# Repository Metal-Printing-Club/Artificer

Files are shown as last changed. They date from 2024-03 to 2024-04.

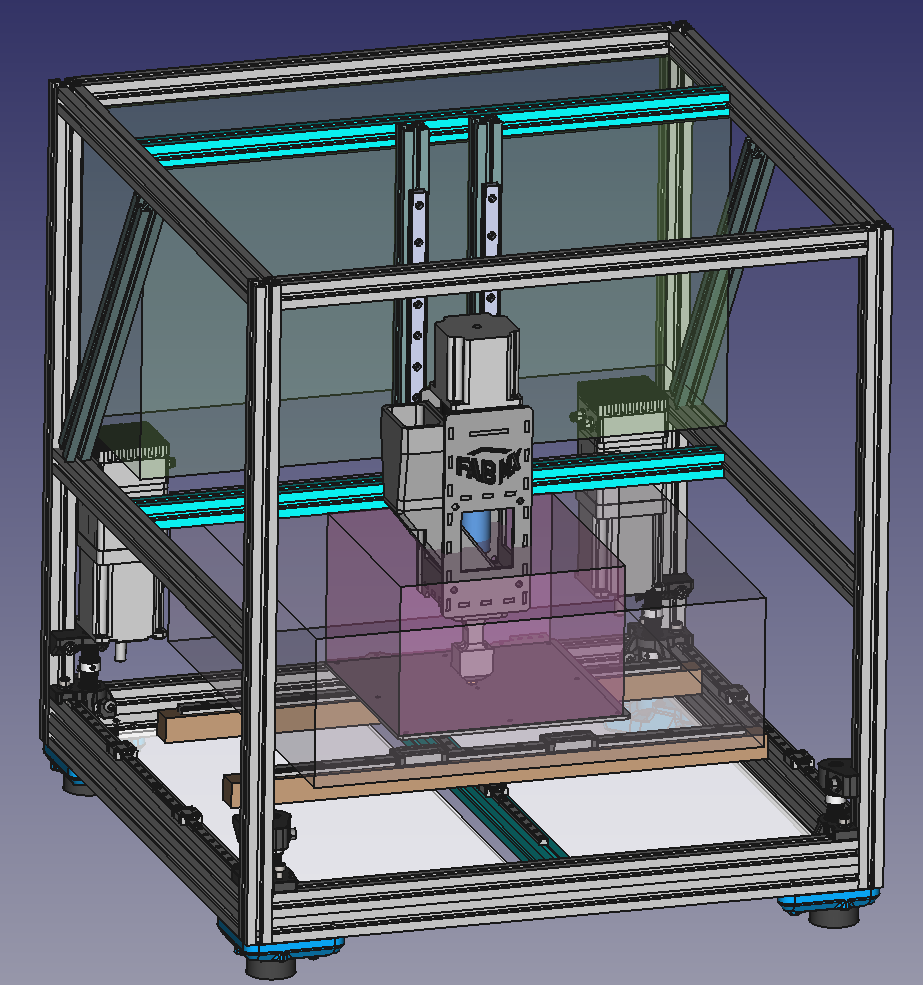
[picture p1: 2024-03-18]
printer-dev/Screenshot 2024-03-17 101501.png

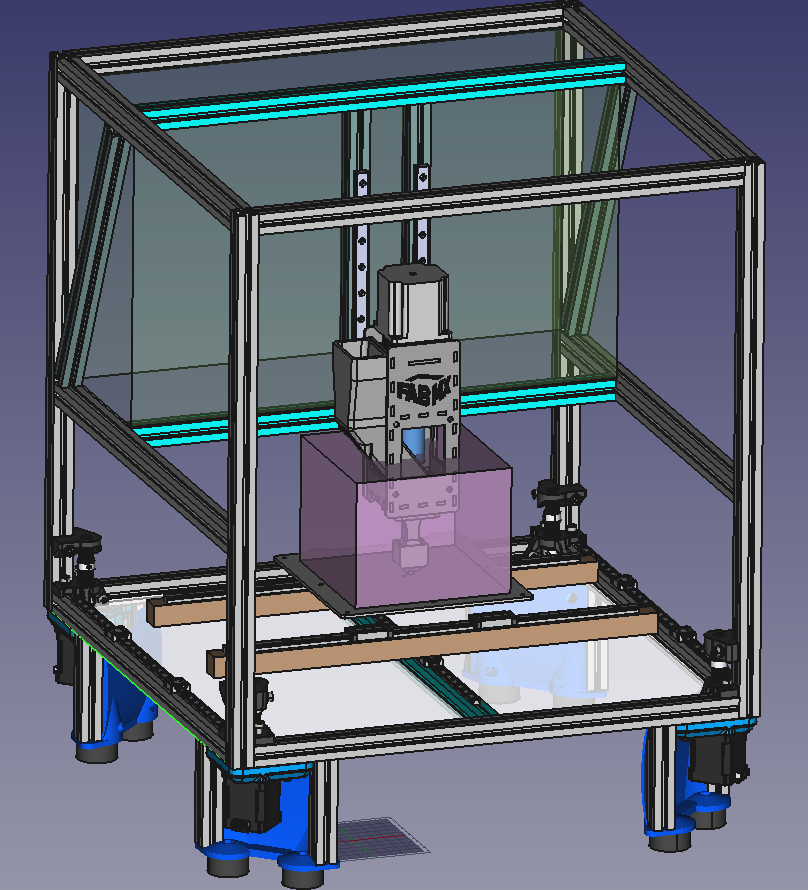
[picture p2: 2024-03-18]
printer-dev/Screenshot 2024-03-14 174216.png

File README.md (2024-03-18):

# Artificer

This is a 3D printer developed at Makespace in Cambridge.

It is primarily intended as a development platform for the FabMX extruder.

The goal is to deliver high precision motion when printing with a very heavy toolhead using affordable and readily-available parts.

We will steal as much as possible from other open hardware projects such as Voron.

The printer should have a build volume of at least 120mm cube. The printer must have a heated bed. Ideally, the printer should be enclosed. Water cooling of the extruder must be integrated. Print speed doesn't have to be world-beating but it would be nice if it was at least comparable to a modern, stock, "off the shelf" 3D printer such as a Voron 2.4.

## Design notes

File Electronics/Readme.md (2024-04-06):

The current electronics configuration for Artificer is as follows:

## Components

### Control
* Mainboard: [Duet 3 6HC v1.01](https://docs.duet3d.com/Duet3D_hardware/Duet_3_family/Duet_3_Mainboard_6HC_Hardware_Overview)
* Expansion: 2x [Duet 3 Motor23CL](https://docs.duet3d.com/en/Duet3D_hardware/Duet_3_family/Duet_3_Motor_23CL)
* Display : [Paneldue 5i](https://docs.duet3d.com/Duet3D_hardware/Accessories/PanelDue)

### Motion

* Extruder Motor: 23HS22-2804S-PG15
* Z motor: 23HE22-2804S
* A/B Motors: Duet 3 Motor 23CL
* XY endstop: Voron Microswitch XY Endstop PCB
* Z endstop: Zmax limit swithc model TBC
* Nozzle touch off switch: Voron Sexbolt
* Z probe: _details TBC_

### Heating

* Extruder Heaters: 2x Generic 6x30-24V 40W, controled as 1x 80W heater
* Extruder thermistor: MF52B 100K B3590

### Cooling
* Extruder Coldside cooling: 12V water pump _details TBC_
* Part cooling blower : _details TBC_
* Electornics bay cooling: _details TBC_
* Other cooling: _details TBC_

##Wiring

The Duet 3 6HC wiring diagram is available on Duet 3D's documentation site, use the v1.01 version:
https://docs.duet3d.com/Duet3D_hardware/Duet_3_family/Duet_3_Mainboard_6HC_Hardware_Overview#wiring-diagram

reproduced below


Annotated image to follow, for now connect as follows:
### Power
* VIN 24V
* Jumper 24V to heated ben (OUT0) input

### Stepper Drivers
* Z Motor on Driver 0
* E motor on Driver 1
* A/B motos on CAN -Fd bus

### Heaters
* Heated bed OUT0
* Both extruder heater cartidges: OUT1
* heated bed thermistor: temp0
* extruder thermistor: temp1

### Endstops
* X : io2.in and GND
* Y : io3.in and GND
* Z : io4.in and GND

### PanelDue
* IO0 header (UART)

### Fans
TBC
Both banks of fan outouts can be set to 12V however NB 800mA max current draw

### Pump
Always on for now

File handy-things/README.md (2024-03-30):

# Handy things

Source and credits:

PanelDue 5" with PCB version 2 by Morten Nielsen found on https://grabcad.com/library/paneldue-5-with-pcb-version-2-1

Duet3D Nema23 closed loop stepper motor without brake 23CL_v1.0_M23-76-2804 by Tony Lock found at https://github.com/Duet3D/Duet3-M23CL/blob/master/v1.0/23CL_v1.0_M23-76-2804.step

FabMX Extuder v3.1 by FabMX found at https://wikifactory.com/+fabmxteam/fabmx/file/PelletExtruder/Version3.1/PelletExtruderv3.1.step

Voron Trident 350 by Voron Design et al. found at https://github.com/VoronDesign/Voron-Trident

Annex Engineering Gasherbrum k3 by Annex Engineering et al. found at https://github.com/Annex-Engineering/Gasherbrum-K3

Prusa Mini by Prusa3d found at https://github.com/prusa3d/Original-Prusa-MINI

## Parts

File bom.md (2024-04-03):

# Bill Of Materials (WIP!)

## Extruder

FabMX kit plus printed parts plus...
2x30mm 24V heater
Thermistor
V6 nozzle hardened steel

## Frame

Voron 2.4 350mm frame kit LDO

Allows us to use the full electronics bay, skirts, feet, etc from Voron Trident 350, so BOM for that (e.g. DIN rails etc) as stock.

Additional extrusions:
4x2040 470mm tapped
4x2020 310mm

Lots of plastic

## Electronics

Meanwell LRS-350-24
Meanwell LRS-200-24
Meanwell LRS-50-12
(Meanwell LRS-50-5? Only needed if we add a Pi)

DC-DC SSR (The second 24V PSU is for a heated bed, so that will be controlled with this)

Filtered fused IEC13 mains inlet
240V rocket switch

Duet3D 6HC controller board
(Duet3D toolhead board?)
Duet3D Paneldue 5i

Optional Raspberry Pi and/or controller board from other kits for Klipper experiments (or just to manage the water cooling? Or can we handle that from the Duet board?)

## Water cooling

Chinese water cooling kit, 240x120 radiator, integrated pump/tank, 12V PSU, 2x120mm 12V fan

Pump and tank:

https://www.aliexpress.com/item/1005004210851438.html?spm=a2g0o.order_list.order_list_main.95.61b31802qJqItj

This has a molex connector, like for a PC.

Specification:

Interface: 8mm/0.31" (used for internal diameter: 5.5-6.5mm/0.21-0.25" hose)
Threaded threads: G1/4
Model: water pump
Voltage: 12V
Power power: 19W
Water flow: 800L/h
Lift: 5m/16.4ft
Size:
Water tank +160MM: approx. 83mm+160mm/3.26+6.29"; Whole length: 264mm/10.39"
Outer diameter: 50mm/1.96"
Internal diameter: 40mm/1.57"

240mm radiator:

https://www.aliexpress.com/item/1005003018063623.html?spm=a2g0o.order_list.order_list_main.101.61b31802qJqItj

This has mounting points for fans and a couple of 1/4 inch threaded hose connectors.

2 x GDSTIME 12v 120mm fan

4 x screw to mount radiator to frame.  6-32 imperial thread.  20mm?

8 x screw to mount fans to radiator.  6-32 imperial thread.  30mm?

Tubing, jubilee clips, 1/4mm adapters, 8mm adapters, etc...

## Motors

XY Motors:
Nema23 - using Duet3D "Duet 3 Motor23 CL" (without brake)

Z motor:
Generic Nema 23

Extruder motor:

Like this from StepperOnline:

    Manufacturer Part Number: 23HS22-2804S-PG47
    Motor Type: Bipolar Stepper
    Step Angle: 0.039deg
    Holding Torque without Gearbox: 1.25Nm(177.01oz.in)
    Rated Current/phase: 2.8A
    Phase Resistance: 0.9ohms
    Inductance: 2.5mH ± 20%(1KHz)

Gear box between this (1:47) or as low as 1:10.

Can probably use a gear ratio as low as 1:2 safely with PolyMIM but we overspec this to experiment with other materials confidently.

## Bed

Prusa Mini 24v heated bed (magnetic, with integrated PCB heater and flat surface)
Prusa mini removeable PEI coated flexible steel sheet

## Motion

X:

Voron 430mm carbon fiber gantry tube x 2
Fysetc hollow rail MGN9 400mm x 2 + MGN9H carriage x 3

y:

400mm MGN7 x 3 + MGN7C carriage x 6

Need to design a special mounting part to attach these rails to the 2020 extrusions.

9mm belts in "Voron belt path" but with strange tensioning and motor mounts and very strange carriage.

z:

250mm MGN12H x 2
250mm lead screw et al.

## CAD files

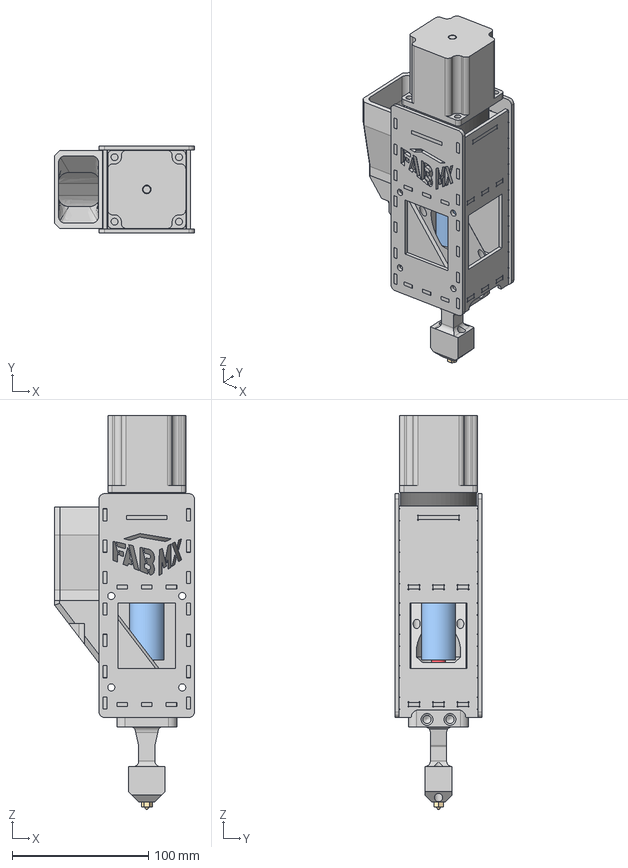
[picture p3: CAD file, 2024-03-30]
handy-things/PelletExtruderv3.1.step
102.7 x 64.0 x 288.8 mm
1fe10484-9e8a-11ee-95c5-028037ec0200_part
1fe12b84-9e8a-11ee-9896-028037ec0200_part
1fe12b85-9e8a-11ee-919e-028037ec0200_part
1fe12b86-9e8a-11ee-9747-028037ec0200_part
1fe12b87-9e8a-11ee-9325-028037ec0200_part
1fe12b88-9e8a-11ee-9519-028037ec0200_part
1fe12b89-9e8a-11ee-aabd-028037ec0200_part
1fe12b8a-9e8a-11ee-bf9c-028037ec0200_part
1fe12b8b-9e8a-11ee-9e8c-028037ec0200_part
PelletInlet_Funnel
E3D V6 Nozzle (0.4mm)
NEMA23 Motor
Getriebe
ShaftCoupler
10mm Extruder Screw (nicht exakt)

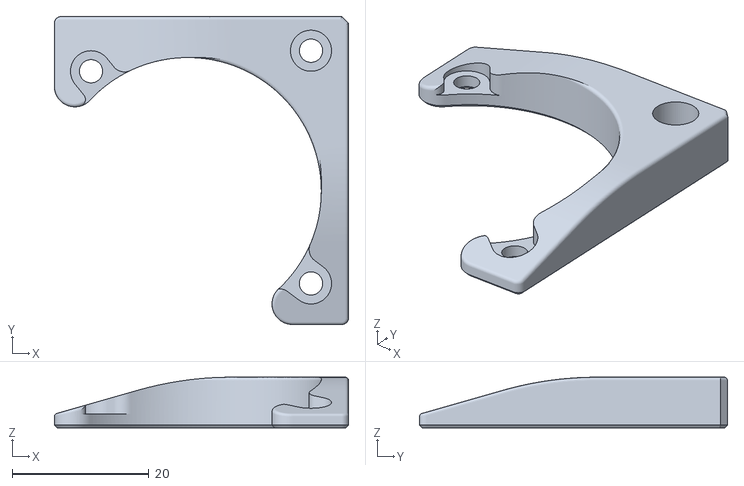
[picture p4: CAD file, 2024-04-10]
printer-dev/subassemblies/feet/[a]_corner_baseplate_a_x2.stl
43.0 x 45.0 x 7.40

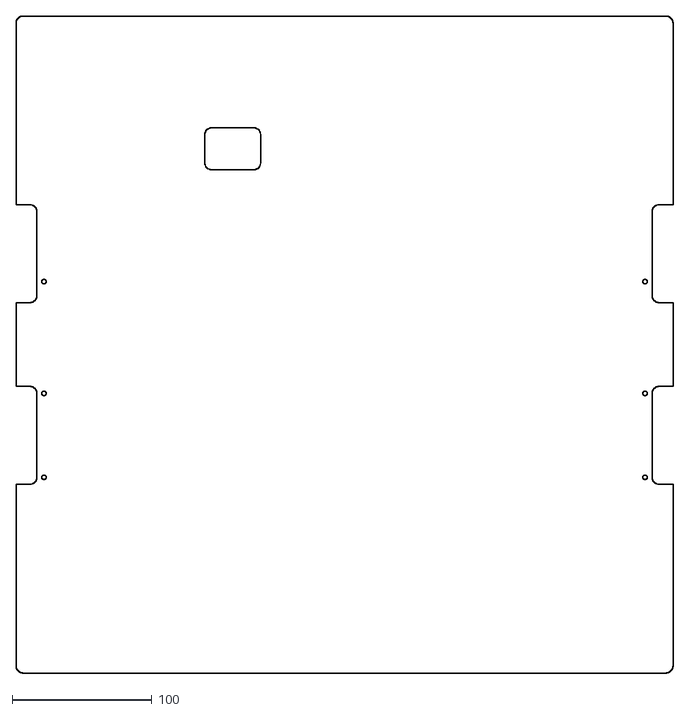
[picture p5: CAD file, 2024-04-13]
printer-dev/subassemblies/panels/deck.dxf
470.0 x 470.0

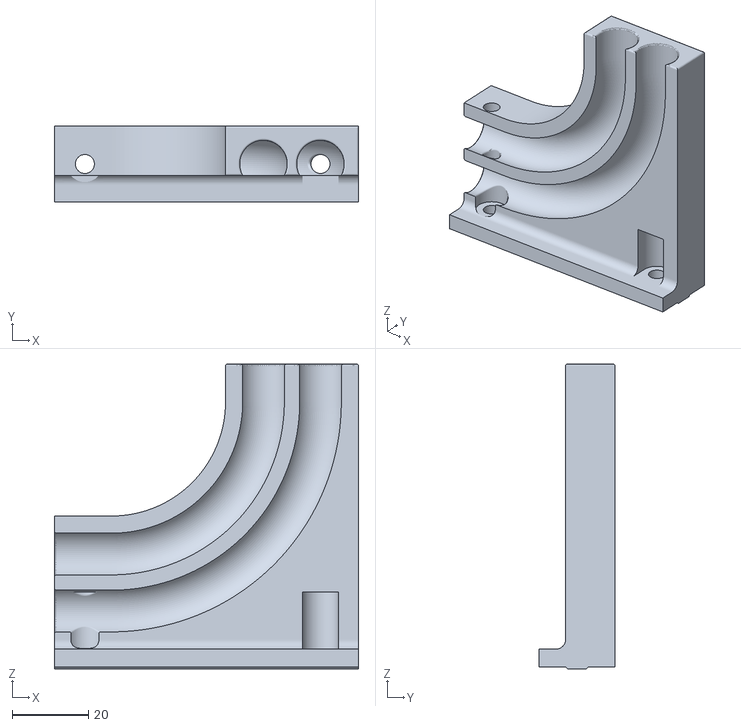
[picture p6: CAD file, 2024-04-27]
printer-dev/subassemblies/watercooling/PipeMountAndBend.stl
80.0 x 20.0 x 80.2

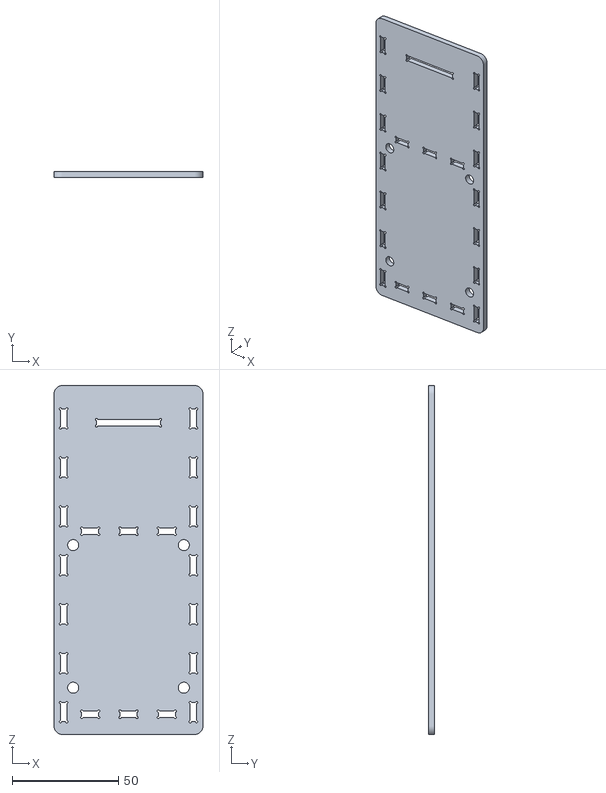
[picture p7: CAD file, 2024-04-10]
printer-dev/subassemblies/z/cad/mock_extruder-back.stl
70.0 x 3.00 x 164.0

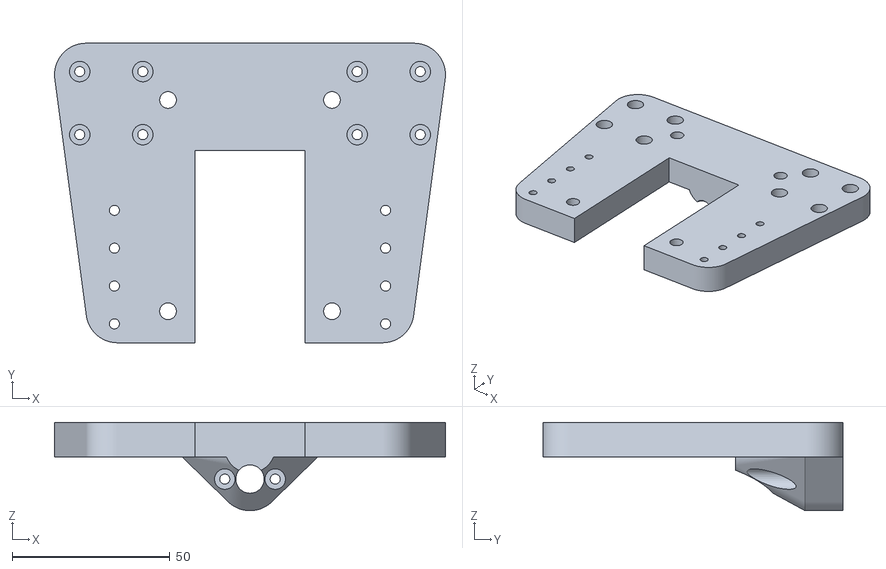
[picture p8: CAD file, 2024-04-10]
printer-dev/subassemblies/z/z-carriage-v2.stl
124.0 x 95.0 x 28.0

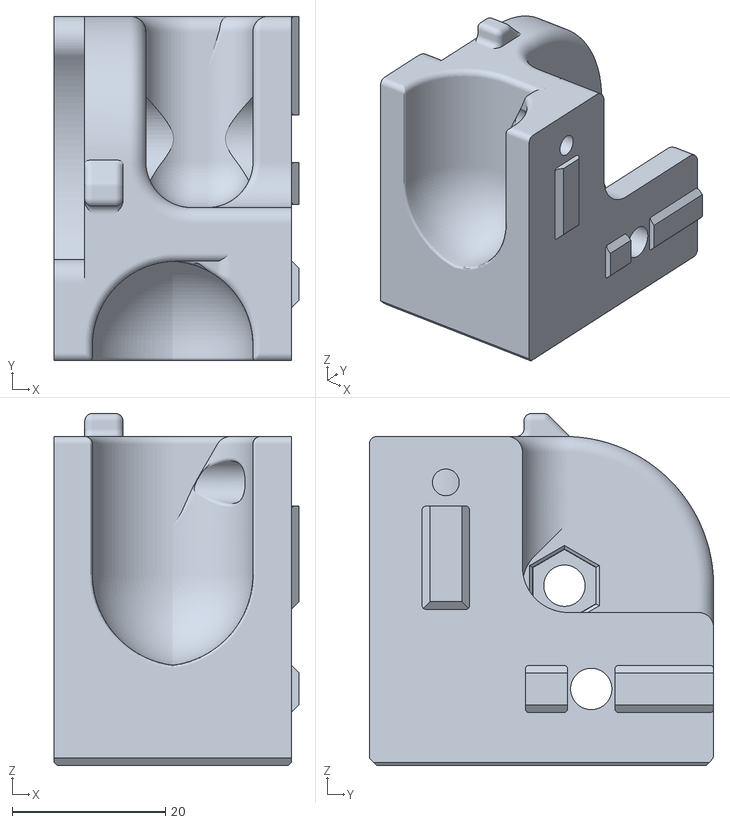
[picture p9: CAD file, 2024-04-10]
printer-dev/subassemblies/feet/corner_a_mod.stl
32.0 x 45.0 x 46.0

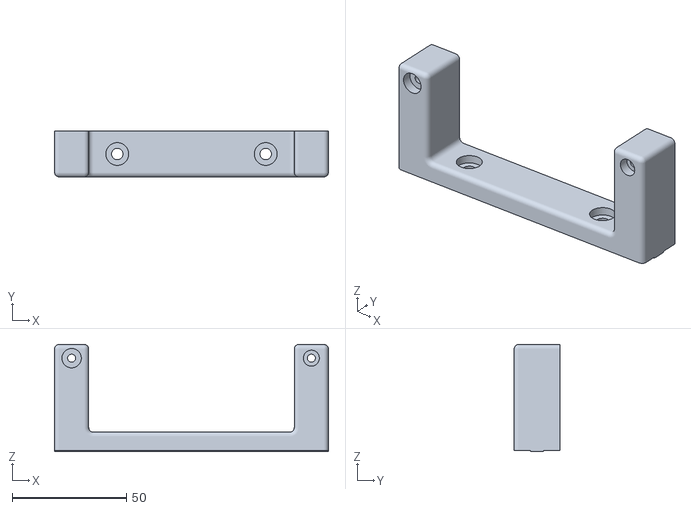
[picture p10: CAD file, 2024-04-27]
printer-dev/subassemblies/watercooling/RadiatorBottom.stl
120.0 x 20.0 x 46.9

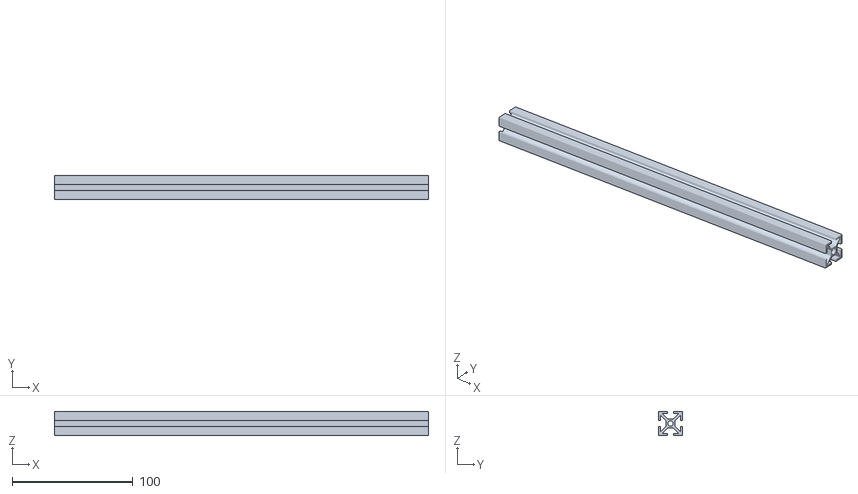
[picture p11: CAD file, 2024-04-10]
printer-dev/subassemblies/z/cad/mock_310-vert.stl
310.0 x 20.0 x 20.0

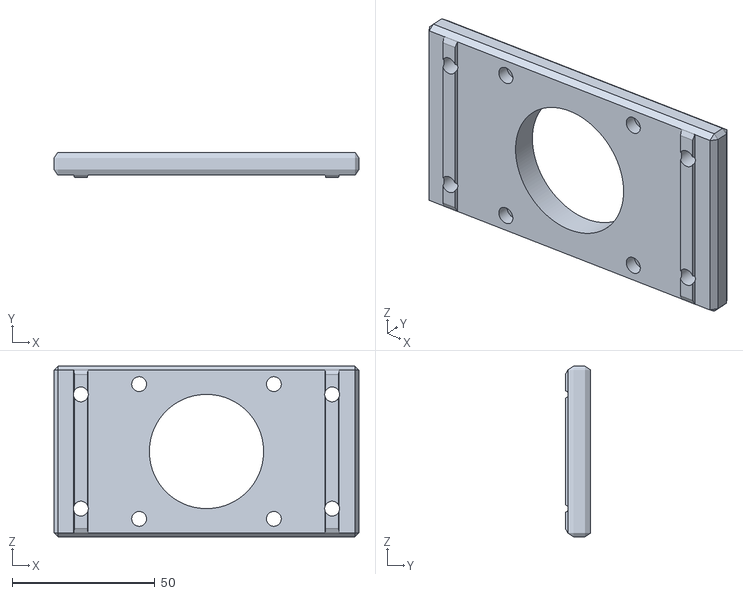
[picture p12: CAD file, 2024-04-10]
printer-dev/subassemblies/z/z-motormount-v2.stl
106.8 x 8.85 x 59.8

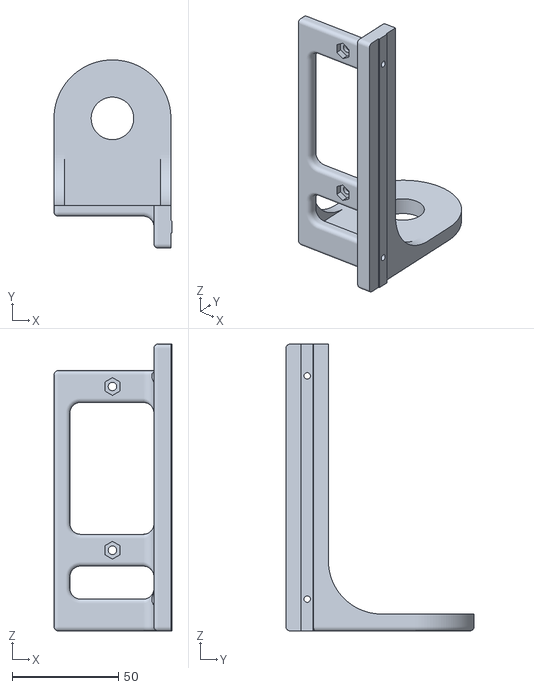
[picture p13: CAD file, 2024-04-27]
printer-dev/subassemblies/watercooling/WaterPumpMount.stl
55.5 x 88.5 x 135.0

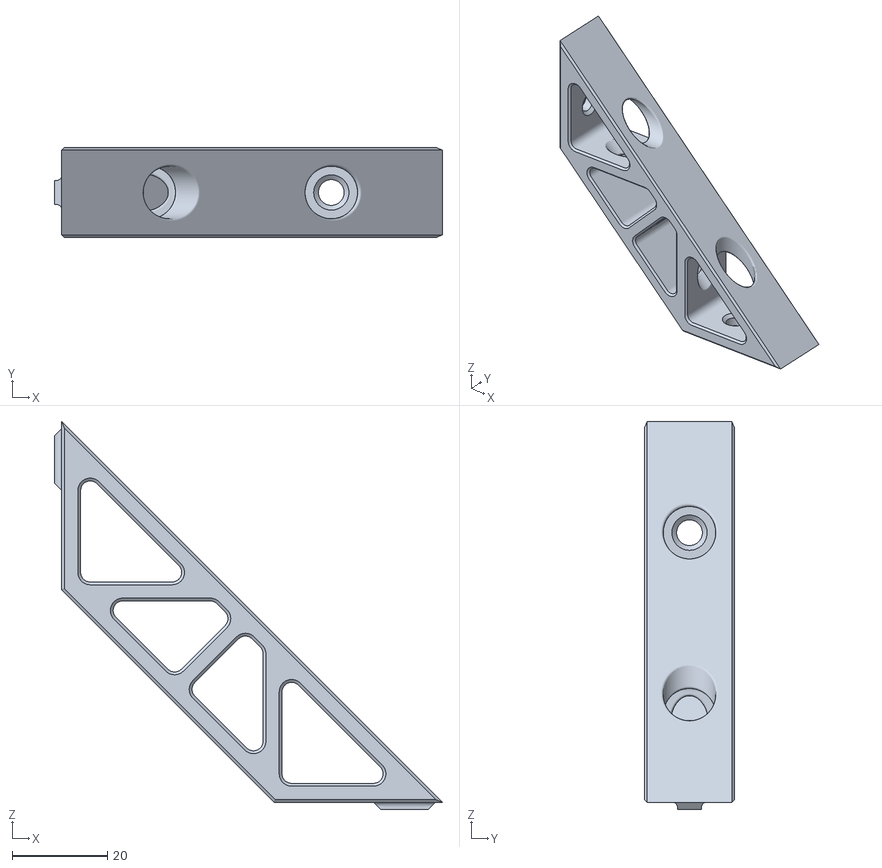
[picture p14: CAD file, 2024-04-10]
printer-dev/subassemblies/z/2020 Bracket.stl
81.5 x 19.0 x 81.5

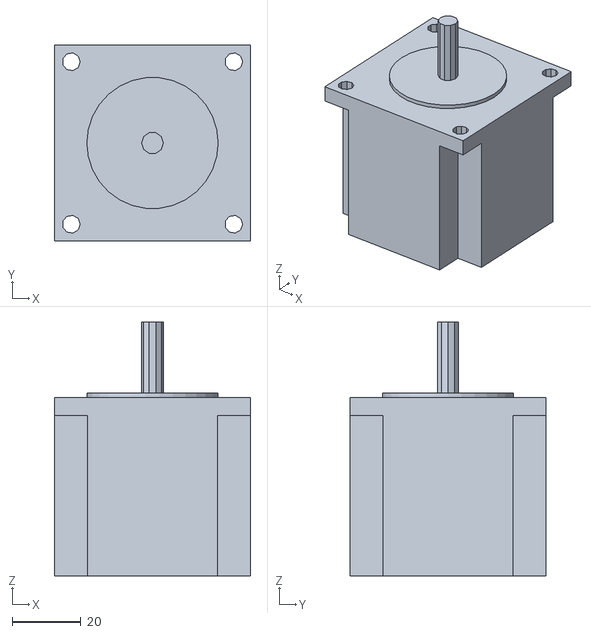
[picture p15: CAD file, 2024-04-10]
printer-dev/subassemblies/z/cad/mock_NEMA23.stl
56.9 x 56.9 x 73.7

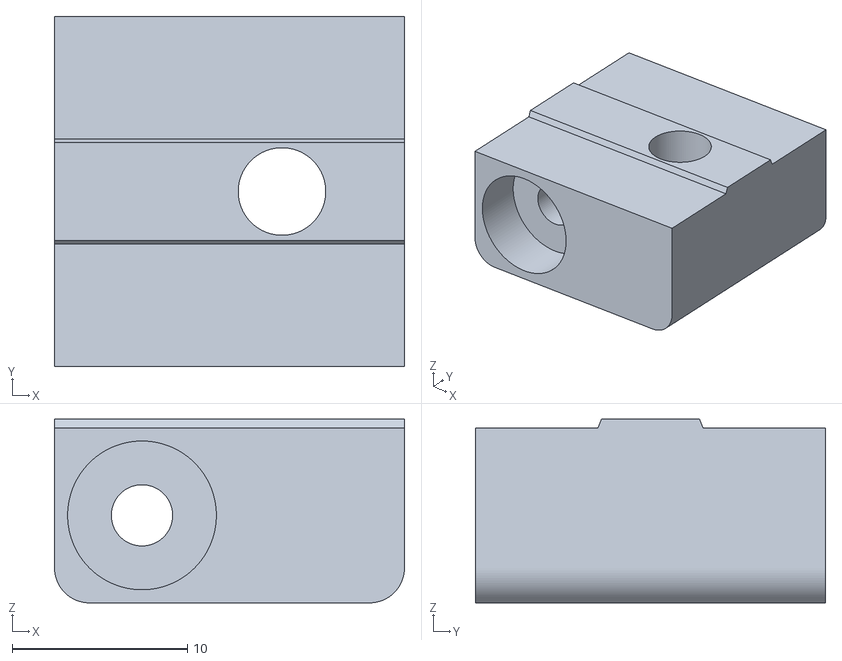
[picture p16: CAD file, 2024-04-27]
printer-dev/subassemblies/watercooling/RadiatorTop.stl
20.0 x 20.0 x 10.5

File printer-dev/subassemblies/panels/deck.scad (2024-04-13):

projection(cut = false) {

//translate([-20,-152.5,185])
//rotate([0,90,0])
//import("corner_a_x2.stl");
difference() {
hull() {
translate([-230,-230,0])
color("pink")
cylinder(d=10,h=2,$fn=64,center=true);

translate([230,230,0])
color("pink")
cylinder(d=10,h=2,$fn=64,center=true);

translate([-230,230,0])
color("pink")
cylinder(d=10,h=2,$fn=64,center=true);

translate([230,-230,0])
color("pink")
cylinder(d=10,h=2,$fn=64,center=true);
}

translate([-215,-35 - 60,0])

cylinder(d=3.2,h=20,$fn=64,center=true);

translate([-215,-35,0])

cylinder(d=3.2,h=20,$fn=64,center=true);


translate([-215,45,0])

cylinder(d=3.2,h=20,$fn=64,center=true);



translate([215,-35 - 60,0])

cylinder(d=3.2,h=20,$fn=64,center=true);

translate([215,-35,0])

cylinder(d=3.2,h=20,$fn=64,center=true);


translate([215,45,0])

cylinder(d=3.2,h=20,$fn=64,center=true);


hull() {
translate([-225,-35 - 60,0])
cylinder(d=10,h=20,$fn=64,center=true);
translate([-225,25 -60,0])
cylinder(d=10,h=20,$fn=64,center=true);

translate([-250,-35 -60,0])
cylinder(d=10,h=20,$fn=64,center=true);
translate([-250,25 -60,0])
cylinder(d=10,h=20,$fn=64,center=true);
}


hull() {
translate([-225,35 + 60,0])
cylinder(d=10,h=20,$fn=64,center=true);
translate([-225,-25 +60,0])
cylinder(d=10,h=20,$fn=64,center=true);

translate([-250,35 +60,0])
cylinder(d=10,h=20,$fn=64,center=true);
translate([-250,-25 +60,0])
cylinder(d=10,h=20,$fn=64,center=true);
}


hull() {
translate([225,-35 - 60,0])
cylinder(d=10,h=20,$fn=64,center=true);
translate([225,25 -60,0])
cylinder(d=10,h=20,$fn=64,center=true);

translate([250,-35 -60,0])
cylinder(d=10,h=20,$fn=64,center=true);
translate([250,25 -60,0])
cylinder(d=10,h=20,$fn=64,center=true);
}


hull() {
translate([225,35 + 60,0])
cylinder(d=10,h=20,$fn=64,center=true);
translate([225,-25 +60,0])
cylinder(d=10,h=20,$fn=64,center=true);

translate([250,35 +60,0])
cylinder(d=10,h=20,$fn=64,center=true);
translate([250,-25 +60,0])
cylinder(d=10,h=20,$fn=64,center=true);
}

//pass through
translate([-130,130,0]){
hull() {
translate([-10,-5,0])
cylinder(d=10,h=20,center=true,$fn=64);

translate([-10,5,0])
cylinder(d=10,h=20,center=true,$fn=64);

translate([10,5,0])
cylinder(d=10,h=20,center=true,$fn=64);

translate([10,-5,0])
cylinder(d=10,h=20,center=true,$fn=64);
}
}
}

}

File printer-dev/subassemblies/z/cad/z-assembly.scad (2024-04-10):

motor_extrusion_channel_width = 5;

module carriage_bits() 
{
color("blue")
translate([44,62,-12.5])
rotate([90,0,0])
translate([0,0,200])
import("mock_MGN12H-LINEAR-GUIDE-BLOCK.stl");

//// carriage
color("blue")
translate([-44,62,-12.5])
rotate([90,0,0])
translate([0,0,200])
import("mock_MGN12H-LINEAR-GUIDE-BLOCK.stl");

color("cyan")
translate([0,36,-12])
//rotate([0,90,0])
import("mock_klf08.stl");

color("cyan")
translate([0,250+35,-12])
rotate([180,0,0])
import("mock_klf08.stl");

color("cyan")
translate([-836.5,-364,119.6])
rotate([90,0,0])
rotate([0,90,0])
import("mock_310-vert.stl");

color("cyan")
translate([-748.5,-364,119.6])
rotate([90,0,0])
rotate([0,90,0])
import("mock_310-vert.stl");

color("blue")
translate([-44,167,-12.5])
rotate([90,0,0])
import("mock_mgn12-rail.stl");

color("blue")
translate([44,167,-12.5])
rotate([90,0,0])
import("mock_mgn12-rail.stl");

/*
color("orange")
translate([44,36,-12.5])
rotate([180,0,0])
import("[a]_z_rail_stop_x3.stl");

color("orange")
translate([-44,36,-12.5])
rotate([180,0,0])
import("[a]_z_rail_stop_x3.stl");
*/

color("cyan")
translate([0,-14,-24])
rotate([90,0,180])
import("mock_extruder-back.stl");

// T8 lead screw
color("cyan")
translate([0,160,-12])
rotate([90,0,0])
cylinder(d=8,h=250,$fn=32,center=true);

color("cyan")
translate([0,330,-48])
cube([200,20,20],center=true);
color("cyan")
translate([0,244,-12])

translate([0,0,-90])
rotate([90,0,180])

import("NEMA23.stl");
}




module mgn12h_holes() {
translate([10,10,0])
cylinder(d=3.2,h=20,center=true,$fn=32);

translate([-10,10,0])
cylinder(d=3.2,h=20,center=true,$fn=32);

translate([10,-10,0])
cylinder(d=3.2,h=20,center=true,$fn=32);

translate([-10,-10,0])
cylinder(d=3.2,h=20,center=true,$fn=32);
}

module mgn12h_wide_holes() {
translate([10,10,0])
cylinder(d=6.5,h=10,center=true,$fn=32);

translate([-10,10,0])
cylinder(d=6.5,h=10,center=true,$fn=32);

translate([10,-10,0])
cylinder(d=6.5,h=10,center=true,$fn=32);

translate([-10,-10,0])
cylinder(d=6.5,h=10,center=true,$fn=32);
}







module accessory_holes() {
translate([0,6,0])
cylinder(d=3.2,h=20,center=true,$fn=32);

translate([0,-6,])
cylinder(d=3.2,h=20,center=true,$fn=32);

}

module accessory_wide_holes() {
translate([0,6,0])
cylinder(d=5.2,h=10,center=true,$fn=32);

translate([0,-6,0])
cylinder(d=5.2,h=10,center=true,$fn=32);
;
}







module fabmx_holes_for_insert() {
//lower hole
//translate([34.667,0,0])
translate([26,0,0])
cylinder(d=5.3,h=18,center=true,$fn=64);

//upper hole
translate([26,67,0])
cylinder(d=5.3,h=18,center=true,$fn=64);

//lower hole for insert
translate([26,0,-4.2])
cylinder(d=6.7,h=10,center=true,$fn=64);

//upper hole for insert
translate([26,67,-4.2])
cylinder(d=6.7,h=10,center=true,$fn=64);

translate([44,66,0])
mgn12h_holes();

translate([44,66,5])
mgn12h_wide_holes();




translate([43,2,0])
accessory_holes();

translate([43,2,-6])
accessory_wide_holes();

translate([43,26,0])
accessory_holes();

translate([43,26,-6])
accessory_wide_holes();

}
module carriage() 
{

//mount
translate([0,171,-12])

scale([1,-1,1])
{
difference() {
translate([0,92,0])
hull() {
rotate([90,0,0])
cylinder(d=20,h=12,$fn=128,center=true);
translate([0,0,10])
cube([44,12,5],center=true);

translate([0,22,10])
rotate([90,0,0])
cylinder(d=16,h=12,$fn=128,center=true);
}
rotate([90,0,0])
cylinder(d=9,h=250,$fn=32,center=true);

translate([8,0,0])
rotate([90,0,0])
cylinder(d=3.2,h=250,$fn=32,center=true);

translate([-8,0,0])
rotate([90,0,0])
cylinder(d=3.2,h=250,$fn=32,center=true);

translate([0,220,0]){
translate([8,0,0])
rotate([90,0,0])
cylinder(d=6.5,h=250,$fn=32,center=true);

translate([-8,0,0])
rotate([90,0,0])
cylinder(d=6.5,h=250,$fn=32,center=true);
}

}
}

difference() {
color("pink")
hull() {

translate([-52,75,0.5])
cylinder(d=20,h=11,$fn=128,center=true);

translate([52,75,0.5])
cylinder(d=20,h=11,$fn=128,center=true);

translate([-42,0,0.5])
cylinder(d=20,h=11,$fn=128,center=true);

translate([42,0,0.5])
cylinder(d=20,h=11,$fn=128,center=true);
}

// mock oldham
//translate([0,95,0])
//cube([35,40,40],center=true);

// mock oldham
translate([0,10,0])
cube([35,82,40],center=true);





fabmx_holes_for_insert();

scale([-1,1,1])
fabmx_holes_for_insert();
}

module coupler_holes() {
translate([-10,35,0])
cylinder(d=5.3,h=11,$fn=64,center=true);

translate([-10,95,0])
cylinder(d=5.3,h=11,$fn=64,center=true);


translate([10,35,0])
cylinder(d=5.3,h=11,$fn=64,center=true);

translate([10,95,0])
cylinder(d=5.3,h=11,$fn=64,center=true);
}
}



module base_bolts() {

translate([27,40,6])
cylinder(d=9.8,h=76,$fn=32,center=true);

translate([27,40,6])
cylinder(d=5.2,h=90,$fn=32,center=true);


translate([-27,40,6])
cylinder(d=9.8,h=76,$fn=32,center=true);

translate([-27,40,6])
cylinder(d=5.2,h=90,$fn=32,center=true);
}

module base() {
difference() {
translate([0,40,-28])
cube([67.8,20,20],center=true);
translate([0,50,-12])
hull() {
rotate([90,0,0])
cylinder(d=30,h=28,$fn=128,center=true);

translate([-20,0,0])
rotate([90,0,0])
cylinder(d=12,h=28,$fn=128,center=true);

translate([20,0,0])
rotate([90,0,0])
cylinder(d=12,h=28,$fn=128,center=true);


}

base_bolts();

translate([0,57,-28])
rotate([30,0,0])
cube([68,20,40],center=true);

}


difference() {
translate([0,33,-12])
cube([67.8,6,12],center=true);



translate([0,50,-12])
{
rotate([90,0,0])
cylinder(d=9,h=48,$fn=128,center=true);

translate([-18,0,0])

rotate([90,0,0])
cylinder(d=5.2,h=48,$fn=128,center=true);

translate([-18,-18,0])

rotate([90,0,0])
cylinder(d=10.5,h=4.2,$fn=6,center=true);




translate([18,0,0])

rotate([90,0,0])
cylinder(d=5.2,h=50,$fn=128,center=true);

translate([18,-18,0])

rotate([90,0,0])
cylinder(d=10.5,h=4.2,$fn=6,center=true);

}

base_bolts();
}

difference() {
hull() {
translate([-44,36,-13])
cube([20,12,10],center=true);


translate([-32,34,-12])
cube([10,8,12],center=true);
}

translate([-44,36,6])
cylinder(d=9.8,h=40,$fn=32,center=true);

translate([-44,36,6])
cylinder(d=5.2,h=60,$fn=32,center=true);

base_bolts();

}


difference() {
hull() {
translate([44,36,-13])
cube([20,12,10],center=true);


translate([32,34,-12])
cube([10,8,12],center=true);
}

translate([44,36,6])
cylinder(d=9.8,h=40,$fn=32,center=true);

translate([44,36,6])
cylinder(d=5.2,h=60,$fn=32,center=true);


base_bolts();

}

}



module top() {



difference() {

hull() {
translate([0,40,-16])
cube([67.8,20,6],center=true);



translate([0,50,-12])
{

translate([-18,-2,0])

rotate([90,0,0])
cylinder(d=11,h=4.2,$fn=64,center=true);

translate([0,-2,0])

rotate([90,0,0])
cylinder(d=28,h=4.2,$fn=64,center=true);

translate([18,-2,0])

rotate([90,0,0])
cylinder(d=11,h=4.2,$fn=64,center=true);


}

}


translate([0,50,-12])
{
rotate([90,0,0])
cylinder(d=9,h=48,$fn=128,center=true);

translate([-18,0,0])

rotate([90,0,0])
cylinder(d=5.2,h=48,$fn=128,center=true);

translate([-18,-18,0])

rotate([90,0,0])
cylinder(d=10.5,h=24.2,$fn=6,center=true);




translate([18,0,0])

rotate([90,0,0])
cylinder(d=5.2,h=50,$fn=128,center=true);

translate([18,-18,0])

rotate([90,0,0])
cylinder(d=10.5,h=24.2,$fn=6,center=true);

}

}





difference() {
hull() {
translate([-44,36,-13])
cube([20,12,10],center=true);


translate([-24,34,-17.95])
cube([10,8,0.1],center=true);
}

translate([-44,36,6])
cylinder(d=9.8,h=40,$fn=32,center=true);

translate([-44,36,6])
cylinder(d=5.2,h=60,$fn=32,center=true);

}


difference() {
hull() {
translate([44,36,-13])
cube([20,12,10],center=true);


translate([24,34,-17.95])
cube([10,8,0.1],center=true);
}

translate([44,36,6])
cylinder(d=9.8,h=40,$fn=32,center=true);

translate([44,36,6])
cylinder(d=5.2,h=60,$fn=32,center=true);



}




translate([-16,4,16])
rotate([0,90,0])
difference() {
hull() {
translate([44,36,-13])
cube([20,20,10],center=true);


translate([34,34,-17.95])
cube([10,8,0.1],center=true);
}

translate([44,36,6])
cylinder(d=9.8,h=40,$fn=32,center=true);

translate([44,36,6])
cylinder(d=5.2,h=60,$fn=32,center=true);



}

scale([-1,1,1])
translate([-16,4,16])
rotate([0,90,0])
difference() {
hull() {
translate([44,36,-13])
cube([20,20,10],center=true);


translate([34,34,-17.95])
cube([10,8,0.1],center=true);
}

translate([44,36,6])
cylinder(d=9.8,h=40,$fn=32,center=true);

translate([44,36,6])
cylinder(d=5.2,h=60,$fn=32,center=true);



}



}

// end of top

module motor_mount() {
difference() {
translate([0,251 ,-102])

hull() {
//cube([108,8,60],center=true);

translate([108/2 - 2,0,28.5])
rotate([0,45,0])
hull() {
translate([0,-3.95,0])
cube([0.1,0.1,0.1],center=true);

cube([2,4,2],center=true);

translate([0,3.95,0])
cube([0.1,0.1,0.1],center=true);
}


translate([108/2 - 2,0,-28.5])
rotate([0,45,0])
hull() {
translate([0,-3.95,0])
cube([0.1,0.1,0.1],center=true);

cube([2,4,2],center=true);

translate([0,3.95,0])
cube([0.1,0.1,0.1],center=true);
}
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

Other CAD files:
printer-dev/subassemblies/z/cad/mock_MGN12H-LINEAR-GUIDE-BLOCK.stl
printer-dev/subassemblies/z/z-base-v2.stl
printer-dev/subassemblies/z/cad/mock_mgn12-rail.stl
printer-dev/subassemblies/z/z-top-v2.stl

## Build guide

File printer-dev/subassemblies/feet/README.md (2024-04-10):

Shorter feet, use the same mounting hardware and Adam Hall rubber feet as Voron Trident.

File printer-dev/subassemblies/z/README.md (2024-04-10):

How to make a Z

Ingredients:

310mm (vertical) 2020 extrusion x 2
100mm (horizontal, for motor) 2020 x 2
250mm MGN12 rail x 2
MGN12H linear guide block x 2
250mm lead screw
NEMA23 motor, 8mm output shaft
M5 nuts x 8
M5 bolts x 16
M5 heat set inserts x 4
M3 heat set inserts x 8
KFL08 bearing blocks x 2
16 x M5 roll-in channel nuts
6 x Openbuilds bracket corners and/or other connecting braces and corners
8 x M3 socket head bolts ~8mm to connect the MGN12H carriage blocks to the printed carriage
~20 x M3 bolts ~6mm to connect the rails to the vertical extrusions~
~20 x M3 T nuts to bolt down the rails
T8 lead screw with follower nut
Oldham coupling for lead screw follower
M3 nuts and bolts to connect the oldham and carriage to the lead screw via the follower.
20T and 40T GT2 6mm pulleys, 8mm bore, with grub screws.
~200mm closed loop GT2 6mm belt to connect the pulleys

Printed:

1 x z-base.stl
1 x z carriage.stl
1 x z-motormount.stl
1 x z-top.stl
2 x 2020 Bracket.stl by John C https://www.printables.com/model/498755-2020-extrusion-corner-bracket/files

Optionally, 10 holes worth of https://www.printables.com/model/240337-m3-t-nut-helpers-for-2020-v-slot-extrusion or similar, x 2

Optionally, more printed backets or printed replacements for the openbuilds corners.

Instructions:

Install the heat set inserts in the carriage.

Attach the carriage to the oldham coupling and the lead screw nut to the oldham coupling. Thread the lead screw through the whole assembly.

Slide the 40T pulley over the lead screw above the top of the carriage. Slide the closed loop belt over, too, so it is just hanging from the lead screw.

Loosely bolt the KLF08 bearings to the z-base and z-top prints using M5 bolts and M5 nuts.

Bolt the bottom print to the bottom of the 310mm vertical extrusions using M5 bolts and channel nuts.
The bottom of the print should be level with the bottom ends of the rails.

Lightly mount the rails to the extrusions, using M3 nuts and bolts, bottoming out at the top of the base bracket.
Don't torque them down, let them slide.

Place the carriage on top of the rails, and insert the bottom of the lead screw into the KLF08 bearing on the z-base.

Lightly bolt the z-top to the top of the extrusions, bottoming it out on the top of the rails, and inserting the top of the lead screw into the top KLF08 bearing.The sequence should now be:

z-top
top KLF08 bearing
top of lead screw with pulley and belt on it
lead screw follower nut
oldham coupling
carriage
bottom of lead screw
lower KLF08
z-base

Bolt the carriage print to the MGN12 carriages using M3 socket head bolts. When it moves freely, and the bottom is square, bolt everything down except the 40t pulley.

Mount the 100mm extusions sticking out from the back of the 310mm extrusions. Use brackets to brace them from underneath.

Attach the NEMA23 to the 100mm extusions using the motor mount. It should be able to slide forward and backwards when it is not bolted down.

Secure the 20T pulley to the output shaft of the NEMA23 with grub screws and thread lock.

Slide the motor mount forward so you can pass the closed loop belt over both the pulleys. Now everything can be alligned vertically, and you can secure the 40T pulley to the lead screw with brub screws (and thread lock!).

Attach the whole assembly to the top and middle central 470mm cross-braces of the frame.

Slide the motor mount back, away from the lead screw, and torque down the M5 bolts to add tension to the Z motor coupling belt.

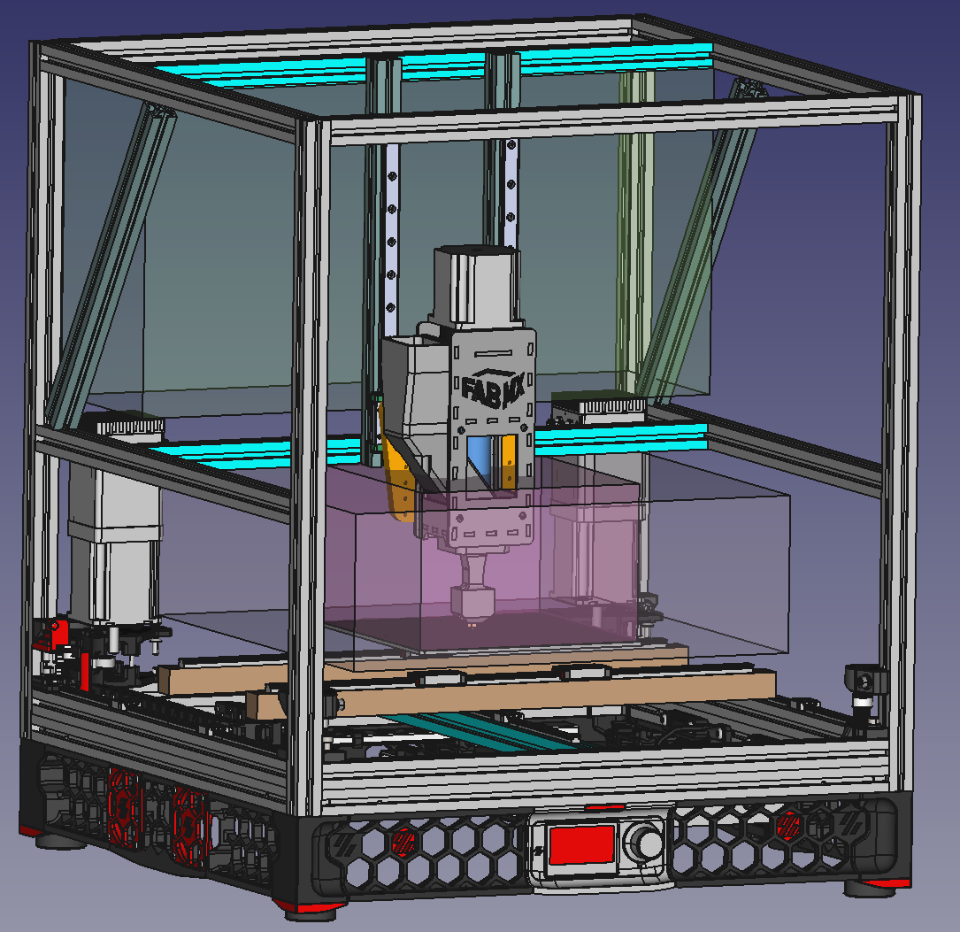
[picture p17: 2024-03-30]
printer-dev/Screenshot 2024-03-30 141504.png

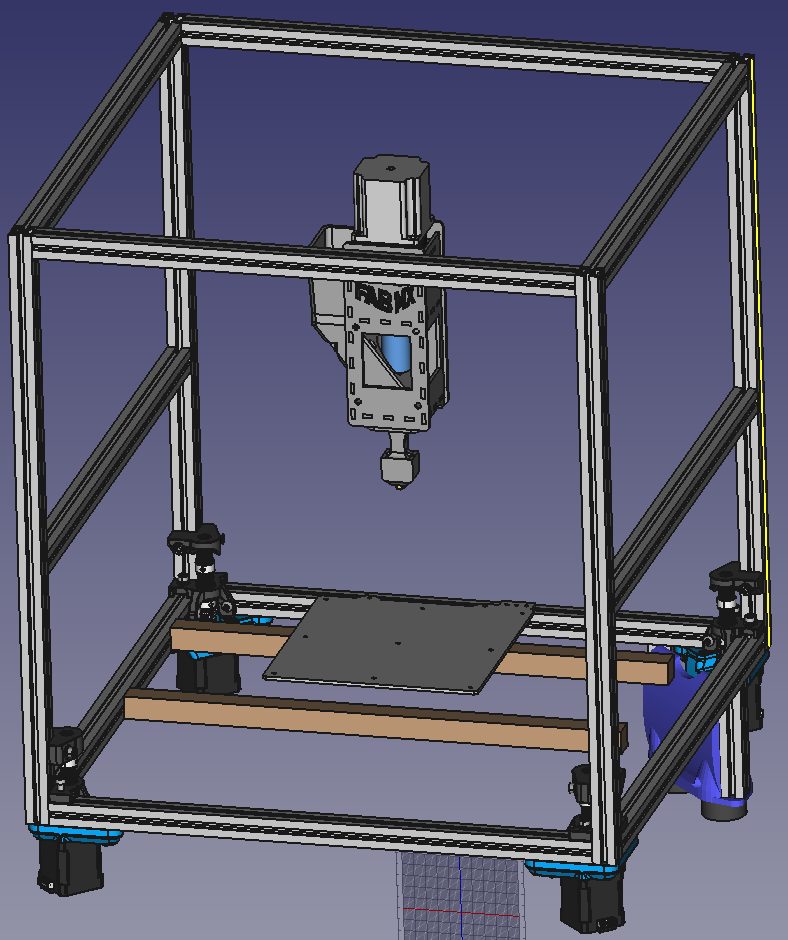
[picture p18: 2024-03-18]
printer-dev/Screenshot 2024-03-12 171413.png

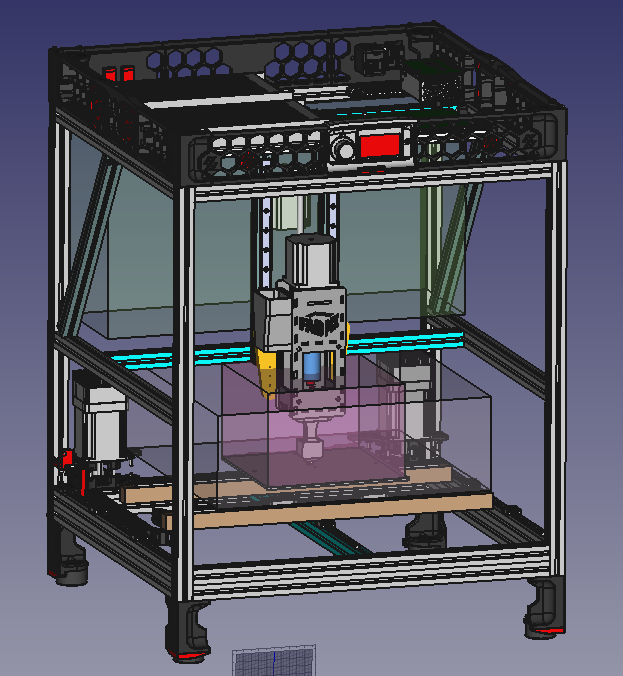
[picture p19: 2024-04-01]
printer-dev/Screenshot 2024-04-01 171859.png

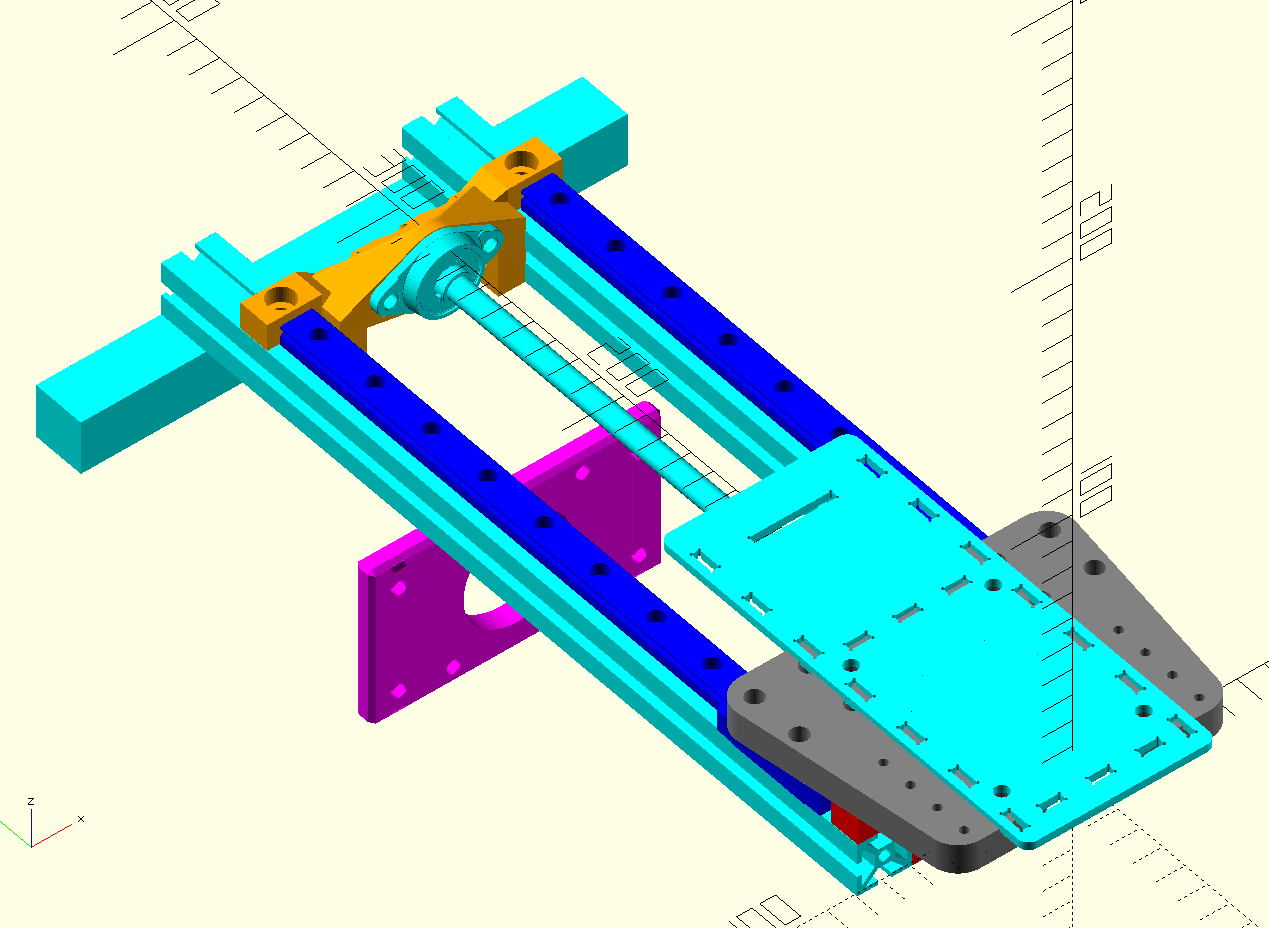
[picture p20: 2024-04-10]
printer-dev/subassemblies/z/Screenshot 2024-04-10 102517.png

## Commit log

2024-03-18 Added some WIP printer development thoughts.
2024-03-30 Add some source material.
    [PelletExtruderv3.1.step]
2024-03-30 Latest WIP CAD snapshot
2024-04-01 Latest printer development snapshot
2024-04-02 Added waterpump support
    [WaterPumpSupport001.stl]
2024-04-03 Update bom.md with screws spec
2024-04-09 Water cooling updates
    [PipeMountAndBend.stl, RadiatorBottom.stl, RadiatorTop.stl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]
2024-04-10 Add z and feet
    [2020 Bracket.stl, [a]_corner_baseplate_a_x2.stl, corner_a_mod.stl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]
2024-04-13 Deck panel for laser cutting
    [deck.dxf, deck.scad]
